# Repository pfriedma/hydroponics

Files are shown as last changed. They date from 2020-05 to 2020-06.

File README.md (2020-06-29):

# hydroponics
A very DIY hydroponic system

FYI: The code is messy and I'll try and clean it up a bit in future commits. 

This work was entirely inspired by [Eleooo]( http://eliooo.com/) and because I'm a huge nerd, I decided to apply microcontrollers. 

The system I ended up building is a hybrid "continuous flow" and "ebb/flow" system - the solution circulates for 15 min every hour, refreshing the solution in the "standard" grow tanks, and "watering" the ebb/flow tank. Because of how the standard tanks are connected together, the pump can't run continuously or they'll overflow, hence the arduino control which runs the pump 20 seconds of every minute for 15 minutes. (Pictures in the diagram folder to come). 

I opted for this model to support growing root veggies like carrots. 

## Construction
### Overview
You have a reservoir which will hold the nutrient solution. A pump pulls the solution and delivers it to the top most container. Solution flows through the containers and drains back into the reservoir.

When flowing horizontally, be aware of height, you'll want to slightly elevate the "upstream" container or else the solution won't flow properly. 
### Materials
* Plastic containers (ideally opaque to prevent algae growth) which will be the planters, and a larger one for the reservoir
* Lids for the containers
* Vinyl tubing
* Hose connectors (see 3d files)
* Aeration pump
* Fluid pump (immersible) x2 (one to purge system)
* Nutrient solution (I've been using General Hydroponics Flora Series)
* Hydroponic Expanded clay pebbles or other substrate of your choice
* Hydroponic baskets (to hold the pebbles and plants)
* LED Grow lights (I chose yellow/white color ones for aesthetics)
* Marine adhesive for waterproofing and securing the connectors

#### Control system materials
* Arduino MKR Wifi 1010 (you can also use a ESP8266). Network connectivity is recommended for NTP and telemetry
* 4 channel relay board with opto-isolator drivers (if you're using a 3.3v microcontroller you'll use separate trigger (3.3v) and coil (5v) voltages. You can pull the 5v supply from the Arduino's pin if you're powering it via a USB supply.
* 4 120v outlets (or a power-strip you can modify)
* PH meter for PH feature
* PH control system (TODO)

### Steps

#### Overview
1. Print connectors (optional)
1. Drill or melt holes in containers (for the hose connectors) and lids (for the plant baskets). You'll want about 6-8cm clearance between baskets, depending on basket size and the plants you intend to grow.
1. Insert baskets into holes
1. Put a bead of adhesive on flange, insert connector, bead the screw-on flange, and screw on (screw goes on outside of container)
1. Arrange containers as needed
1. For containers that drain vertically (down), you'll want to cut a bit of tubing to put on the inside of the container to ensure the fluid level is just touching the bottom of the baskets
1. Hook up the tubing
1. Set up lights and plug everything in (make sure that each device - pump, lights, air pump - are plugged into their appropriate outlet) 
1. Place pump in reservoir, connect, fill reservoir with water and test. Depending on your setup, you'll want to adjust the pump runtime per cycle (`PUMP_PULSE_LENGTH`) in `src/constants_and_pins.h` 
1. Transplant plants into baskets, covering with washed clay pebbles. 
1. Follow nutrient manufacturer's guides

#### Control system
1. Select 4 appropriate digital I/O pins for the relay board and connect 
1. Make sure if using a 3.3 v board, the jumper that bridges signal and coil voltages on the relay control board is removed. You'll supply 5v separately. 
1. Connect ground
1. Connect 5v to relay coil input VCC
1. Load up Arduino IDE and Modify `constants_and_pins.h` with the pins chosen 
1. Flash and test. 
1. Wire up outlets to the relay board. I recommend testing each outlet against the controller with a continuity tester before supplying voltage

## Repository Structure
### 3d files
This dir contains an OpenSCAD file which can generate STL files for the various types of hose connectors used. There is a function which will also generate bulkhead connectors with a threaded washer. 

3d printing may be much less expensive for you, as hardware stores sell the connectors for about $5-8 each!

You'll want to experiment with your print settings to achieve a water-tight print. I found with my Ender3, a 150% extrusion at .16 layer-height, solid infill was decent. You'll likely have to do some tests.

The two functions you probably care about are 
> print_connector_part(num=2, flanged=true);

and

>print_flange_screw();

Specify the diameter of your tubing (OD) , and print away! The default OD in the OpenSCAD file is 16.25mm.

### src
This directory contains the Arduino source for the control system. This was implemented on a MKR WIFI1010 and relies on Wifi and NTP to work correctly. HOWEVER, you can use a much simpler device as long as it has a reasonably reliable clock. You'll just need to add code and a user interface for setting the time. 

All output pins are connected to a relay control board (mine's a 5v coil, 3v trigger) which then switch the 120v pumps and lighting. The pH pumps are 12v but also need relays. If you've got a 6 or 8-channel relay board, you can use the one board, just be careful about mixing up the 12 VDC and 120 VAC ;) 

### diagrams
TBD. This directory will contain wiring and other diagrams describing the physical layout of the system.

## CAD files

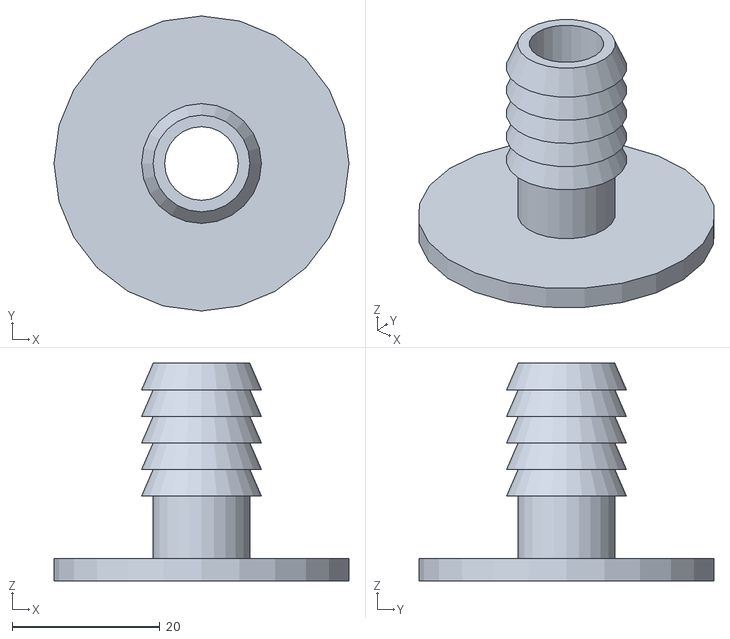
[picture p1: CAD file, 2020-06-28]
3d Files/flanged_connector1.stl
40.0 x 40.0 x 29.5

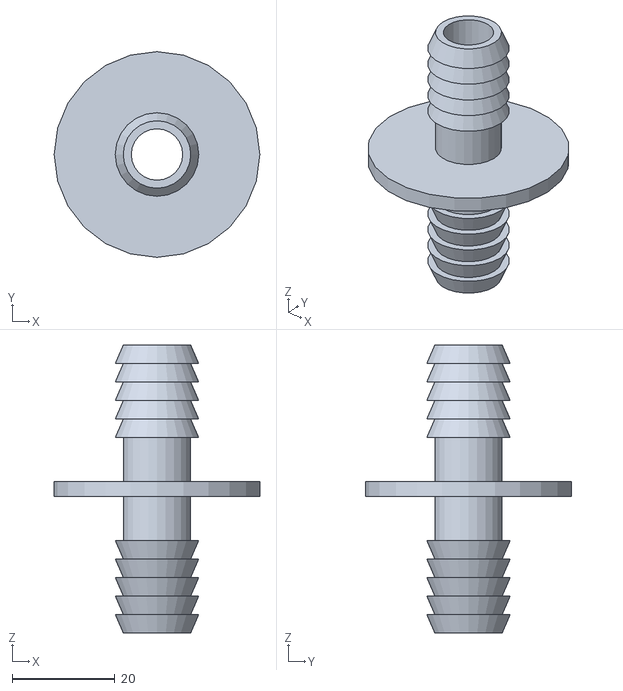
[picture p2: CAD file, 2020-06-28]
3d Files/flanged_connector2.stl
40.0 x 40.0 x 56.0

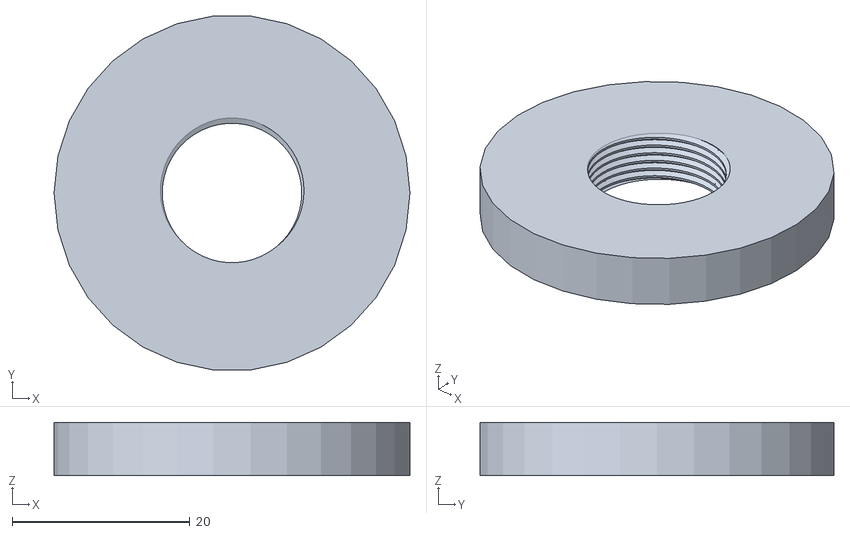
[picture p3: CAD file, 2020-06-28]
3d Files/flanged_connector_ring.stl
40.0 x 39.8 x 6.00

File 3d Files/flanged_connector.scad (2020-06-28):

// Module loads
include <threads.scad>;

overlap = 0.001;

OD = 16.25;
OR = OD/2;

ID = 10;
IR = ID/2;
flange_height = 3;
conetop = IR+((OR-IR)/2);

length = 18;
sections = 5;
section_length = length/(sections);
//standoff = section_length;
standoff=10;

/* 
Select how many connector ends by setting 'num' to an integer between 1 and 5 for best results
If you want a flange on the connector, use flanged=true
*/
print_connector_part(num=2, flanged=true);

//print_flange_screw();
// Helper Print Statements
//print_cone_section();
//print_cone_sections();
//print_single_connector($fn=24);
//print_flanged_connector(3, $fn=24);

//print_connectors(2, $fn=24);
//print_connectors(3, $fn=24);
//print_connectors(4, $fn=24);
//print_connectors(5, $fn=24);
//print_connectors(6, $fn=24);
//print_connectors(8, $fn=24);

//print_elbow($fn=24);
//print_elbow(angle=45, $fn=24);
//print_elbow(angle=120, $fn=24);

module print_connector_part(num=1, flanged=false)
{
    if (flanged==true) {
        print_flanged_connectors(num, $fn=24);
    } else {
        if (num == 1) {
            print_single_connector($fn=24);
        } else {
            print_connectors(num, $fn=24);
        }
    }
}

module print_cone_section()
{
	conebottom = OR;

	difference()
	{
		cylinder(r1=conebottom, r2=conetop, h=section_length+overlap);
	
		translate([0,0,-overlap])
		cylinder(r=IR, h=section_length+overlap*3);
	}
}

module print_cone_sections()
{
	for (section = [0:sections-1])
	{
		translate([0,0,section*section_length])
		print_cone_section();
	}
}

module connector_blank()
{
	cylinder(r=IR, h=standoff+overlap*3);
	sphere(r=IR);
}
module print_flanged_connectors(num)
{
    if (num==1) {
        print_single_connector();
    } else {
        print_connectors(num);
    }
    
    if (num>2) {
        translate([0,0,standoff])
            if (num <= 4) 
                flange(IR);
    } else {
      flange(IR);
    }
}

module print_flange_screw()
{
    difference(){
        cylinder(r=IR*4, h=flange_height*2, center=true);
       translate([0,0,-flange_height*2+1])
        metric_thread(OD+.5,1,flange_height*3, internal=true);
    }
    
}


module print_single_connector()
{
	translate([0,0,standoff-overlap])
	print_cone_sections();

	difference()
	{
		cylinder(r=conetop, h=standoff);
        
		translate([0,0,-overlap])
       
		connector_blank();
       
	}
    metric_thread(OD,1,standoff);
    
}
module flange(ir)
{
    difference()
    {
        cylinder(r=ir*4, h=flange_height, center=true);
        cylinder(r=ir, h=6, center=true);
        
        }
    
    

      
}

module print_connectors(num)
{
	angle = 360/num;

	difference()
	{
		union()
		{
			sphere(r=conetop);
			for(connector = [1:num])
			{
				rotate([(connector-1)*angle, 0, 0])
				print_single_connector();
			}
		}

		for(connector = [1:num])
		{
			rotate([(connector-1)*angle, 0, 0])
			connector_blank();
		}
	}

}

module print_elbow(angle=90)
{	
	difference()
	{
		union()
		{
			sphere(r=conetop);

			print_single_connector();
			rotate([angle, 0, 0])
			print_single_connector();
		}

		// subtract out the rounded bottom
		// for each connector
		connector_blank();

		rotate([angle, 0, 0])
		connector_blank();
	}
}

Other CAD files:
3d Files/threads.scad

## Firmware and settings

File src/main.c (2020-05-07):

/*
 Garden Control System 1.0
 This uses an Arduino MKR WIFI 1010
 If you're using a different device, you'll want to change some of the code, specifically around Wifi, Server, and NTP
 If you're using a non-network device, you'll want to add code (and hardware like buttons and a screen) to set the system's clock (for timing, lights, etc)
 
*/

#include <SPI.h>
#include <WiFiNINA.h>
#include <WiFiUdp.h>
#include <RTCZero.h>
#include <utility/wifi_drv.h>
#include "arduino_secrets.h"
#include "constants_and_pins.h"


//Global Variables 
unsigned long health_check = 0;
bool primeMode = false;
unsigned long primeEpoch = 0;
unsigned long phEpoch = 0;
float sysPh = 0.0; 

// PH Voltage conversion (pin voltage / resolution) 
float vConversion = (sysVoltage/adcRes); 

// Lights, Airation, Pump
bool statusArray[3] = {false, false, false};


// Template defs
void printWifiStatus();
void setRtc(unsigned long epoc);
unsigned long getEpoc();
unsigned long sendNTPpacket(IPAddress& address);

// NTP and WIFI Stuff...
///////please enter your sensitive data in the Secret tab/arduino_secrets.h
char ssid[] = SECRET_SSID;        // your network SSID (name)
char pass[] = SECRET_PASS;    // your network password (use for WPA, or use as key for WEP)
int keyIndex = 0;            // your network key Index number (needed only for WEP)
// A UDP instance to let us send and receive packets over UDP
WiFiUDP Udp;
unsigned int localPort = 2390;      // local port to listen for UDP packets
IPAddress timeServer(129, 6, 15, 28); // time.nist.gov NTP server
int status = WL_IDLE_STATUS;
WiFiServer server(80);
const int NTP_PACKET_SIZE = 48; // NTP time stamp is in the first 48 bytes of the message
byte packetBuffer[ NTP_PACKET_SIZE]; //buffer to hold incoming and outgoing packets


// Create a RTC instance
RTCZero rtc;


void setup() {
  // Setup Pins
  setupPins();

  Serial.begin(9600);

  initializeWifi();
  
  // Enable UDP for NTP query
  Udp.begin(localPort);
  // Turn on the real-time clock
  rtc.begin();

  setTimeFromNTP();

  server.begin();

  // We're Up!
  setRGBLed(0, 64, 0);
  digitalWrite(LED_BUILTIN, HIGH);
}


void setupPins() {
  pinMode(lightPin, OUTPUT);
  pinMode(airPin, OUTPUT);
  pinMode(pumpPin, OUTPUT);
  pinMode(purgePin, OUTPUT);
  pinMode(LED_BUILTIN, OUTPUT);
  pinMode(phDownPin, OUTPUT);
  pinMode(phUpPin, OUTPUT);
  pinMode(buttonPin, INPUT);
  pinMode(phMeasurePin, INPUT); 
  digitalWrite(lightPin, PINOFF);
  digitalWrite(airPin, PINOFF);
  digitalWrite(pumpPin, PINOFF);
  digitalWrite(LED_BUILTIN, LOW);
  digitalWrite(phDownPin, PINOFF);
  digitalWrite(phUpPin, PINOFF);
  digitalWrite(purgePin, PINOFF);
}


void initializeWifi() {
  WiFi.setHostname(hostname);

  // check for the WiFi module:
  if (WiFi.status() == WL_NO_MODULE) {
    Serial.println("Communication with WiFi module failed!");
    // don't continue
    while (true) {
      digitalWrite(LED_BUILTIN, HIGH);
      delay(500);
      digitalWrite(LED_BUILTIN, LOW);
    }
  }
  WiFiDrv::pinMode(25, OUTPUT);  //GREEN
  WiFiDrv::pinMode(26, OUTPUT);  //RED
  WiFiDrv::pinMode(27, OUTPUT);  //BLUE

  setRGBLed(0, 0, 64);


  String fv = WiFi.firmwareVersion();
  if (fv < WIFI_FIRMWARE_LATEST_VERSION) {
    Serial.println("Please upgrade the firmware");
  }

  // attempt to connect to Wifi network:
  while (status != WL_CONNECTED) {
    setRGBLed(0, 0, 16);
    Serial.print("Attempting to connect to SSID: ");
    Serial.println(ssid);
    // Connect to WPA/WPA2 network. Change this line if using open or WEP network:
    status = WiFi.begin(ssid, pass);

    // wait 5 seconds for connection:
    for (int i = 0; i <= 5; i++) {
      setRGBLed(0, 0, 64);
      delay(500);
      setRGBLed(0, 0, 16);
      delay(500);
    }
  }

  Serial.println("Connected to wifi");
  printWifiStatus();
  setRGBLed(64, 64, 0);
}

void setTimeFromNTP() {
  Serial.println("\nStarting connection to server...");
  

  unsigned long epoch = getEpoc();
  if (epoch == 0) {
    Serial.println("\n Error getting epoch from NTP\n");
    setRGBLed(128, 0, 0);
  } else {
    Serial.println("Setting RTC...\n");
    setRtc(epoch);
  }
}

void setRtc(unsigned long epoch) {
  
  Serial.print("Epoch received: ");
  Serial.println(epoch);
  rtc.setEpoch(epoch);
  Serial.println();
}

unsigned long getEpoc() {
  sendNTPpacket(timeServer); // send an NTP packet to a time server
  // wait to see if a reply is available
  delay(1000);
  if (Udp.parsePacket()) {
    Serial.println("packet received");
    // We've received a packet, read the data from it
    Udp.read(packetBuffer, NTP_PACKET_SIZE); // read the packet into the buffer

    //the timestamp starts at byte 40 of the received packet and is four bytes,
    // or two words, long. First, esxtract the two words:

    unsigned long highWord = word(packetBuffer[40], packetBuffer[41]);
    unsigned long lowWord = word(packetBuffer[42], packetBuffer[43]);
    // combine the four bytes (two words) into a long integer
    // this is NTP time (seconds since Jan 1 1900):
    unsigned long secsSince1900 = highWord << 16 | lowWord;
    Serial.print("Seconds since Jan 1 1900 = ");
    Serial.println(secsSince1900);

    // now convert NTP time into everyday time:
    Serial.print("Unix time = ");
    // Unix time starts on Jan 1 1970. In seconds, that's 2208988800:
    const unsigned long seventyYears = 2208988800UL;
    // subtract seventy years:
    unsigned long epoch = secsSince1900 - seventyYears;
    return epoch;
  } else {
    return 0;
  }
}

void loop() {
  checkTest();
  checkHelth();
  doPhCheck();
  pollStatus();
  checkPrime();
  setPins();
  processRequest();
  delay(10);
}

void printTime()
{
  print2digits(rtc.getHours());
  Serial.print(":");
  print2digits(rtc.getMinutes());
  Serial.print(":");
  print2digits(rtc.getSeconds());
  Serial.println();
}

// send an NTP request to the time server at the given address
unsigned long sendNTPpacket(IPAddress& address) {
  //Serial.println("1");
  // set all bytes in the buffer to 0
  memset(packetBuffer, 0, NTP_PACKET_SIZE);
  // Initialize values needed to form NTP request
  // (see URL above for details on the packets)
  //Serial.println("2");
  packetBuffer[0] = 0b11100011;   // LI, Version, Mode
  packetBuffer[1] = 0;     // Stratum, or type of clock
  packetBuffer[2] = 6;     // Polling Interval
  packetBuffer[3] = 0xEC;  // Peer Clock Precision
  // 8 bytes of zero for Root Delay & Root Dispersion
  packetBuffer[12]  = 49;
  packetBuffer[13]  = 0x4E;
  packetBuffer[14]  = 49;
  packetBuffer[15]  = 52;

  //Serial.println("3");

  // all NTP fields have been given values, now
  // you can send a packet requesting a timestamp:
  Udp.beginPacket(address, 123); //NTP requests are to port 123
  //Serial.println("4");
  Udp.write(packetBuffer, NTP_PACKET_SIZE);
  //Serial.println("5");
  Udp.endPacket();
  //Serial.println("6");
}


void printWifiStatus() {
  // print the SSID of the network you're attached to:
  Serial.print("SSID: ");
  Serial.println(WiFi.SSID());

  // print your board's IP address:
  IPAddress ip = WiFi.localIP();
  Serial.print("IP Address: ");
  Serial.println(ip);

  // print the received signal strength:
  long rssi = WiFi.RSSI();
  Serial.print("signal strength (RSSI):");
  Serial.print(rssi);
  Serial.println(" dBm");
}

void print2digits(int number) {
  if (number < 10) {
    Serial.print("0"); // print a 0 before if the number is < than 10
  }
  Serial.print(number);
}

void setPins() {
  //Serial.println("\nSetting System to the following state:\n");
  //printStatus();
  runLights(statusArray[0]);
  runAir(statusArray[1]);
  runPump(statusArray[2]);
}

void printStatus() {
  Serial.print("Lights: ");
  Serial.print(onOffText(statusArray[0]));
  Serial.print("Air: ");
  Serial.print(onOffText(statusArray[1]));
  Serial.print("Pump: ");
  Serial.print(onOffText(statusArray[2]));
  Serial.println("\n");

}

String onOffText(bool val) {
  if (val) {
    return "On\n";
  } else {
    return "Off\n";
  }
}

String stringify(bool val) {
  if (val) {
    return "true";
  } else {
    return "false";
  }
}
void runAir(bool on) {
  if (on) {
    digitalWrite(airPin, PINON);
  } else {
    digitalWrite(airPin, PINOFF);
  }
}

void runPump(bool on) {
  byte seconds = rtc.getSeconds();
  if (on) {
    if (seconds < PUMP_PULSE_LENGTH) {
      digitalWrite(pumpPin, PINON);
    } else {
      digitalWrite(pumpPin, PINOFF);
    }
  } else {
    digitalWrite(pumpPin, PINOFF);
  }
}

void runLights(bool on) {
  if (on) {
    digitalWrite(lightPin, PINON);
  } else {
    digitalWrite(lightPin, PINOFF);
  }
}

void pollStatus() {
  byte hour = rtc.getHours();
  byte minute = rtc.getMinutes();
  if (hour == LIGHT_OFF_HOURS && minute >= LIGHT_OFF_MINUTES) {
    setLights(false);
  } else if (hour == LIGHT_OFF_HOURS) {
    if (minute <= LIGHT_OFF_MINUTES){
      setLights(true);
    }
  }
  if ((hour >= LIGHT_ON_HOURS) || (hour >= LIGHT_ON_HOURS && minute >= LIGHT_ON_MINUTES )) {
    setLights(true);
  }

  if (
    (minute >= SYSTEM_RUN_OFFSET && minute <= (SYSTEM_RUN_OFFSET + SYSTEM_RUN_LENGTH + AIR_BUFFER)) || (minute >= AIR_RUN_ADDL && minute <= (AIR_RUN_ADDL + AIR_RUN_ADDL_LEN))) {
    setAir(true);
  } else {
    setAir(false);
  }

  if ((minute >= (SYSTEM_RUN_OFFSET + AIR_BUFFER)) && (minute <= (SYSTEM_RUN_LENGTH + SYSTEM_RUN_OFFSET))) {
    setPump(true);
  } else {
    setPump(false);
  }
}

void processRequest() {
  // listen for incoming clients
  WiFiClient client = server.available();
  if (client) {
    Serial.println("new client");
    // an http request ends with a blank line
    boolean currentLineIsBlank = true;
    String currentLine = "";
    while (client.connected()) {
      if (client.available()) {
        char c = client.read();
        Serial.write(c);
        // if you've gotten to the end of the line (received a newline
        // character) and the line is blank, the http request has ended,
        // so you can send a reply
        if (c == '\n') {
          if (currentLine.length() == 0) {
            // send a standard http response header
            client.println("HTTP/1.1 200 OK");
            client.println("Content-Type: text/json");
            client.println("Connection: close");  // the connection will be closed after completion of the response
            client.println("Refresh: 10");  // refresh the page automatically every 5 sec
            client.println();
            client.print((String)"{\n  \"state\":{\"lights\":" += stringify(statusArray[0]) += (String)", \"air_pump\":" += stringify(statusArray[1]) += (String)", \"fluid_pump\":" += stringify(statusArray[2])  += (String)", \"pH\":" += (String)sysPh += (String)"},\n");
            client.print((String)"  \"systemtime\":{\"hours\":" += (String)rtc.getHours() += (String)", \"minutes\":" += (String)rtc.getMinutes() += (String)", \"seconds\":" += (String)rtc.getSeconds() += (String)"},\n");
            client.print((String)"  \"uptime\":{\"system\":" += (String)millis() += (String)", \"health_counter\":" += (String)health_check += (String)"}\n}\n");

            client.println("\n");
            break;
          } else {
            // you're starting a new line
            currentLine = "";
          }
        }

        else if (c != '\r') {
          // you've gotten a character on the current line
          currentLine += c;
        }
        if (currentLine.endsWith("GET /T")) {
          test();
        }
        if (currentLine.endsWith("GET /PRIME")) {
          primeSystem();
        }
        if (currentLine.endsWith("GET /PURGE")) {
          doPurge();
        }
      }
    }
    // give the web browser time to receive the data
    delay(10);

    // close the connection:
    client.stop();
    Serial.println("client disonnected");
  }
}

void checkTest() {
  int count = 0;
  int limit = 10;
  /*
    if (digitalRead(buttonPin) == LOW) {
    Serial.println("Test mode entered, hold to prime system...\n");
    setRGBLed(0,45,56);
    while (digitalRead(buttonPin) == LOW && count <= limit){
      count++;
      delay(1000);
    }
    if (count > 1 && count < limit/2){
      test();
    }
    if (count >= limit) {
      primeSystem();
    }
    Serial.println("Returning to normalcy...\n");
    setRGBLed(0,64,0);
    } */
}
void test() {
  setRGBLed(0, 64, 64);
  setStatus(false, false, false);
  setPins();
  Serial.println("Test Routine On:\n");
  Serial.println("Lights...\n");
  runLights(true);
  delay(5000);
  runLights(false);
  Serial.println("Air Pump...\n");
  runAir(true);
  delay(5000);
  runAir(false);
  Serial.println("Fluid Pump...\n");
  runPump(true);
  delay(5000);
  runPump(false);
  Serial.println("Complete.\n");
  setRGBLed(0, 64, 0);
}


void setRGBLed(int r, int g, int b) {
  WiFiDrv::analogWrite(25, g);  // for configurable brightness
  WiFiDrv::analogWrite(26, r);  // for configurable brightness
  WiFiDrv::analogWrite(27, b);  // for configurable brightness
}

void primeSystem() {
  setRGBLed(96, 32, 96);
  primeEpoch = rtc.getEpoch() + PRIME_LENGTH;
  primeMode = true;
}

void checkPrime() {
  if (primeMode) {
    setStatus(true, true, true);
    if (rtc.getEpoch() > primeEpoch) {
      primeEpoch = 0;
      primeMode = false;
      setStatus(true, false, false);
    }
  }
}

void halt() {
  setStatus(false, false, false);
}

void setStatus(bool lights, bool airPump, bool fluidPump) {
  if (lights != NULL) {
    statusArray[0] = lights;
  }
  if (airPump != NULL) {
    statusArray[1] = airPump;
  }
  if (fluidPump != NULL) {
    statusArray[2] = fluidPump;
  }
}

void setPump(bool pump){
  statusArray[2] = pump;
}
void setAir(bool air){
  statusArray[1] = air;
}
void setLights(bool lights){
  statusArray[0] = lights;
}

void checkHelth() {
  health_check++;
  if (health_check > HEALTH_LIMIT) {
    doHealthCleanup();
  }

}

void doHealthCleanup() {

  unsigned long epoch = getEpoc();
  if (epoch == 0) {
    Serial.println("\n Error getting epoch from NTP\n");
    setRGBLed(128, 0, 0);
    delay(1000);
  } else {
    setRtc(epoch);
    health_check=0;
  }
}

float getPh() {
  int measurementValue = sampleMeasurementAvg(analogSampleSize, phMeasurePin);
  float adjustedValue = measurementValue * vConversion;
  Serial.println("Measured analog input with average value: " + (String)measurementValue + " and adjusted value of: " + (String)adjustedValue + "\n");
  // pH = adjustedValue * phSensorVoltageScalar; 
  return (float)7.0; 
}

int sampleMeasurementAvg(int sampleSize, int samplePin){
  int measurementArray[sampleSize];
  int sum = 0;
  int avg = 0;
  for (int i = 0; i < sampleSize; i++){
    measurementArray[i] = analogRead(samplePin);
    delay(25);
  }
  // Sum the array, discarding the first N value
  for (int j = discardFirstN; j < sampleSize; j++) {
    sum += measurementArray[j];
  }
  avg = (sum / (sampleSize - discardFirstN)); 
  return avg;
  
}


void doPhCheck() {
  sysPh = getPh();
  Serial.println("Got Ph of: " + (String)sysPh + "\n");
  if ( phEpoch + phUpdateFreq < rtc.getEpoch() ) {
    phAdjust(sysPh);
  }
}

void phAdjust(float ph){
    if ( ph - phThreshold > idealPh ) {
      doPhDown();
      phEpoch = rtc.getEpoch();
      Serial.println("Adjusted pH DOWN \n");
    } else if ( ph + phThreshold < idealPh ) {
      doPhUp();
      phEpoch = rtc.getEpoch();
      Serial.println("Adjusted pH UP \n");
    }
 }

void doPhUp(){
    digitalWrite(phUpPin, PINON);
    delay(500);
    digitalWrite(phUpPin, PINOFF);
}

void doPhDown(){
    digitalWrite(phDownPin, PINON);
    delay(500);
    digitalWrite(phDownPin, PINOFF);
}

void doPurge(){
    digitalWrite(purgePin, PINON);
    delay(20000);
    digitalWrite(purgePin, PINOFF);
}

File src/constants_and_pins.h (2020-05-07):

/* This file contains pin definitions and constants, including:
   - Time (for lights, pump timing, etc)
   - Which pins connect to what hardware
   - Adjustment and scaling variables
   - Desired pH values, etc
*/


// Pin Definitions
const int lightPin = A2;
const int airPin = A3;
const int pumpPin = A4;
const int purgePin = A5;
const int buttonPin = 5;
const int phUpPin = 4;
const int phDownPin = 3;
const int phMeasurePin = A6;

//ADC Values
const float sysVoltage = 3.3;
const float adcRes = 4095.0;
const int analogSampleSize = 10;
const int discardFirstN = 1;

// Ph values 
const float idealPh = 7.0;
const float phThreshold = 1.0;
const float phSensorVoltageScalar = 3.5;




const unsigned long phUpdateFreq = 21600;

// Relay board is low = on
#define PINON LOW
#define PINOFF HIGH

// How long before doing maintence stuff like checking in with NTP
#define HEALTH_LIMIT 1000000

// Network 
const char hostname[16]="garden";


// Timing and schedule (relative to system timezone, so probably UTC)
#define LIGHT_ON_HOURS 10
#define LIGHT_ON_MINUTES 0
#define LIGHT_OFF_HOURS 0
#define LIGHT_OFF_MINUTES 30

// The fluid system (airation and fluid re-circulate)
// runs hourly at the OFFSET from the hour for RUN_LENGTH time.
// Airation will be offset BUFFER minutes in either direction.
// Airation also runs at the specified additional time and length
#define SYSTEM_RUN_OFFSET 0
#define SYSTEM_RUN_LENGTH 15
#define AIR_BUFFER 2
#define AIR_RUN_ADDL 30
#define AIR_RUN_ADDL_LEN 15

// The pump runs for this many seconds every minute
#define PUMP_PULSE_LENGTH 25

// How long should the system run for during a priming (seconds)
#define PRIME_LENGTH 600
